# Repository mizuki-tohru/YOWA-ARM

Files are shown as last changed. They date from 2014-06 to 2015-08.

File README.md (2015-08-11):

YOWA-ARM
========

YOWA-ARM (Weak arm) is a robotic arm that can be used in the side of the human. No strength to hurt a person, this is a weak arm. This can not lift heavy objects. but, for example, push of a button work, only has a light work, is available for these. 
Inexpensive, but YOWA-ARM is a robot arm that could work. It has a working radius of the length of the human arm, and in harmony with the work environment for human beings. YOWA-ARM is not a toy. However, it is very inexpensive.
"How supposing I have one more arm." Do you have any kind of experience?
 YOWA-ARM can also perform the useless work which pushes a button without a repetition rest. 

YOWA-ARM is a specification based on the "Technical guidelines related to safety standards, such as the use of industrial robot, and, notice that define the Japan mechanical Minister of Health, Labour and Welfare pursuant to the provisions of Article 36-31 issue the Ordinance on Industrial Safety and Health".
There is only output of 80 watts or less, and meets the safety measures each. Maximum output does not exceed 150 Newton. Therefore, the safety fence is not required for YOWA-ARM.
Also, as a safety measure, It install a sensor for detecting a human body around the arm tip. Then, the arm will decelerate to avoid the rapid collision of the human body.
Exposes all the design data, YOWA-ARM can be manufactured by anyone.

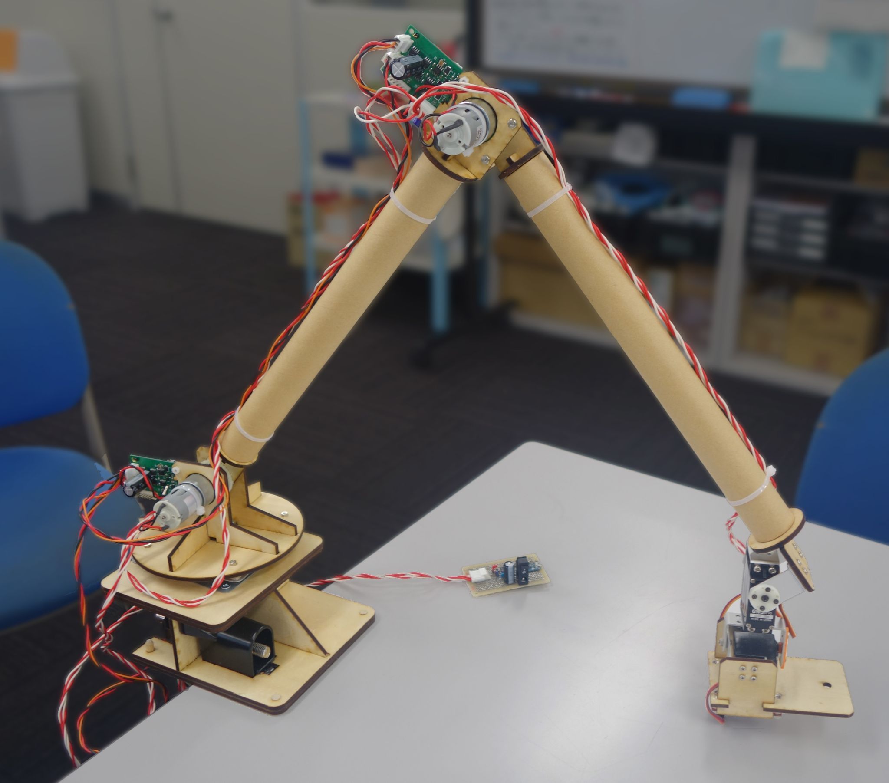
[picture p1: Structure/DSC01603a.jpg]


　YOWA-ARM(よわアーム)は、人間のそばで使えるロボットアームです。人を傷つけるような強さの無い、弱いアームです。重いものを持つことは出来ませんが、ちょっとボタンを押すだけ、とか、ちょっとライトを持っているだけ、といった作業は出来ます。
　YOWA-ARMはできるだけ安価に、でも仕事ができるロボットアームとして設計されました。人間の腕の長さの作業半径を持ち、人間用の作業環境にそのまま調和します。YOWA-ARMはオモチャじゃないロボットアームとしては破格に安価です。
　もう一本、手があったら、この作業もっと楽になるのに。そういう経験ありませんか？この仕事って結局ボタン押すだけ、そういう仕事ありませんか？YOWA-ARMはそういう仕事を疲れることなく繰り返し休み無くおこなえます。

　YOWA-ARMは、産業用ロボットの使用等の安全基準に関する技術上の指針、及び、労働安全衛生規則第三十六条第三十一号の規定に基づき厚生労働大臣が定める機械を定める告示、に基づき、80ワット以下の出力で各安全措置を満たした仕様です。また最大出力は150ニュートンを超えません。そのためこのYOWA-ARMは安全柵が不要です。
　また安全措置として、アーム先端部に周囲の人体を検出するセンサを搭載して、人体への急速な衝突を避けて減速します。
　YOWA-ARMは設計データを全て公開し、誰でも製造可能とします。

========

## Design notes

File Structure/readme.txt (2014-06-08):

Guidance of processing:
Use a plywood board (overlaid plywood, or MDF 4 mm in thickness). 
Data is AUTOCAD R13 ASCII format.

加工の手引き：
シナベニアまたはMDF 厚さ4mmの板を使用します。
データはAUTOCAD R13 ASCIIフォーマットとなっています。

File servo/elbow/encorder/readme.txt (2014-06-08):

Guidance of processing:

This is data of the optical encoder's codewheel of a through slits incremental quadrature type encoder.
To encorder_org_23.dxf which is a reflective slits, you paste together and create encorder_org_24.dxf of a transparent material.
I used the cutting plotter, Silhouette-Cameo for creation.
It reduce data to 1/6 after reading. Please reduce to 46% next after reducing to 36% first.

cutting parameter:
encorder_org_23.dxf
Material: Film label seal Silver thickness 0.07mm 
parameter: speed 4 thickness 7 Cutter 5 

encorder_org_24.dxf
 vinyl chloride board thickness 0.3mm
parameter: speed 1 thickness 24 Cutter 8 

加工の手引き:

これは透過型エンコーダの遮光円盤のデータです。
反射幕であるencorder_org_23.dxfに、透明な素材のencorder_org_24.dxfを張り合わせて作成します。
作成にはカッティングプロッタ、シルエットカメオを使用しました。
データは読み込み後1/6に縮小します。まず36%に縮小してから、次に46%に縮小してください。

加工パラメータは以下の通りです。
encorder_org_23.dxf
素材：エーワン N29283 フィルム・ラベルシール つや消し シルバー
パラメータ：速度4 厚さ7 カッター5

encorder_org_24.dxf
素材：塩ビ板 クリア 0.3mm
パラメータ：速度1 厚さ24 カッター8

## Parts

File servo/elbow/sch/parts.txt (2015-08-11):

Parts list
No				Name			note		number		buyer
U$12			STM32F373C					1			Digi-key
U$10			HEDS9701-C54    Encorder	1			Digi-key
U$5,U$6			IR2302S						2			Digi-key
Q1,Q2,Q3,Q4		FDS5680         FET			4			Akizuki(Akihabara)
U$7,U$17,U$18	4S69F           Inverter	3			Suzushou(Akihabara)
U$8				TAR5SB33		REG			1			Akizuki(Akihabara)
U$15     		NJM78L05UA      REG         1			Akizuki(Akihabara)
U$11			SN65HVD30       RS422drv	1			Digi-key
Q9				NX5032GA 8MHz	XTAL		1			Digi-key
Q10             32.768kHz       XTAL		1			Akizuki(Akihabara)
U$13,U$14       ACPL-M60L                   2			Digi-key
LED3,4      	LED SMD 0603    led			2			Akizuki(Akihabara)
D1,D4 	      	SX34F           diode		2			Akizuki(Akihabara)
D5       		1SS352         	diode		1			Akizuki(Akihabara)
U$16     		ZX62R-B-5P     	USB-MicroB	1			Akizuki(Akihabara)
L1              BLM21PG331SN    			1			Digi-key(or Akizuki)

C24,C25,C26,C27 7pF SMD 0603	cap			4			Suzushou(Akihabara)

C16,C29,C30,C31,C32
		    	0.01uF SMD 0603 cap			5			Sengoku(Akihabara)
C11,C12,C13,C17,C18,C19,C28,C34,C35,C40
       			0.1uF SMD 0603  cap			10			Sengoku(Akihabara)
C39      		0.33uF SMD 0603 cap         1			Suzushou(Akihabara)
C14      		1uF SMD 2012	cap			1			Akizuki(Akihabara)
C15      		4.7uF SMD 2012	cap			1			Akizuki(Akihabara)
C33,C41      	10uF SMD 3216	cap			2			Akizuki(Akihabara)
C6,C7       	22uF SMD 3225   cap			2			Akizuki(Akihabara)
C8  	     	470uF electrolytic cap		1			Sengoku(Akihabara)
R5,R6,R7,R8,R11,R19,R21,C21
				22ƒ¶ SMD 0603	regisiter	8			Sengoku(Akihabara)
R33,R34			27ƒ¶ SMD 0603	regisiter	2			Sengoku(Akihabara)
R23,R24			33ƒ¶ SMD 0603	regisiter	2			Sengoku(Akihabara)
R25	     	 	100ƒ¶ SMD 0603	regisiter	1			Sengoku(Akihabara)
R28				220ƒ¶ SMD 0603	regisiter	1			Sengoku(Akihabara)
R26,R27,R29,R30,R31,R32
			  	330ƒ¶ SMD 0603	regisiter	6			Sengoku(Akihabara)
R36,R37			470ƒ¶ SMD 0603	regisiter	2			Sengoku(Akihabara)
R35				1.5kƒ¶ SMD 0603	regisiter	1			Sengoku(Akihabara)
R1,R10,R22      10kƒ¶ SMD 0603	regisiter	3			Sengoku(Akihabara)

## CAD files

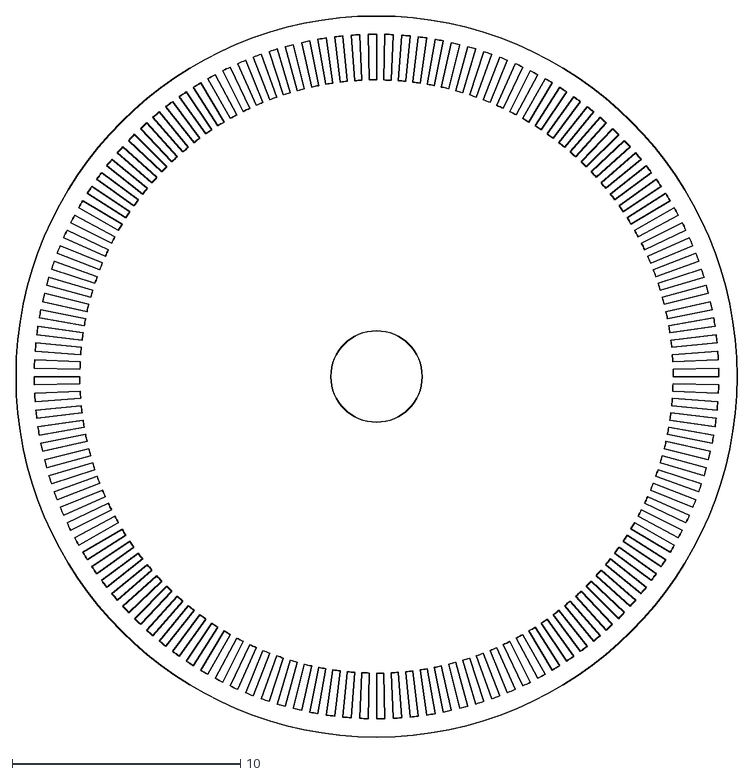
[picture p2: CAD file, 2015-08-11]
servo/elbow/encorder/encorder_org_26a.dxf
31.6 x 31.6

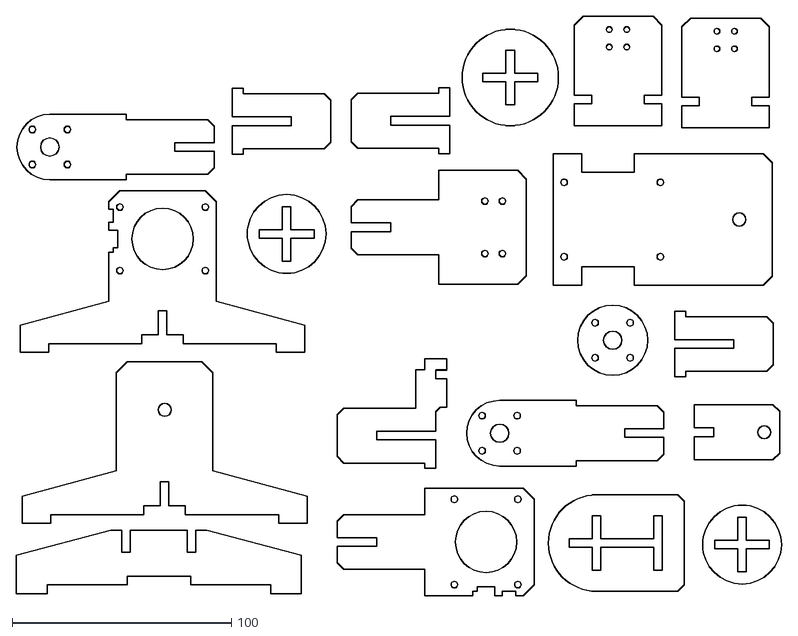
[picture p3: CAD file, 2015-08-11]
Structure/elbow_072_ascii.dxf
349.3 x 264.5

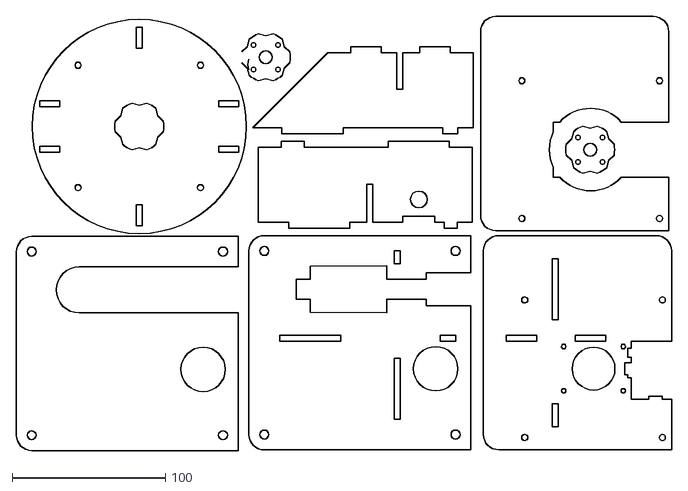
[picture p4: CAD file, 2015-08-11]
Structure/elbow_071a_ascii.dxf
428.2 x 283.7

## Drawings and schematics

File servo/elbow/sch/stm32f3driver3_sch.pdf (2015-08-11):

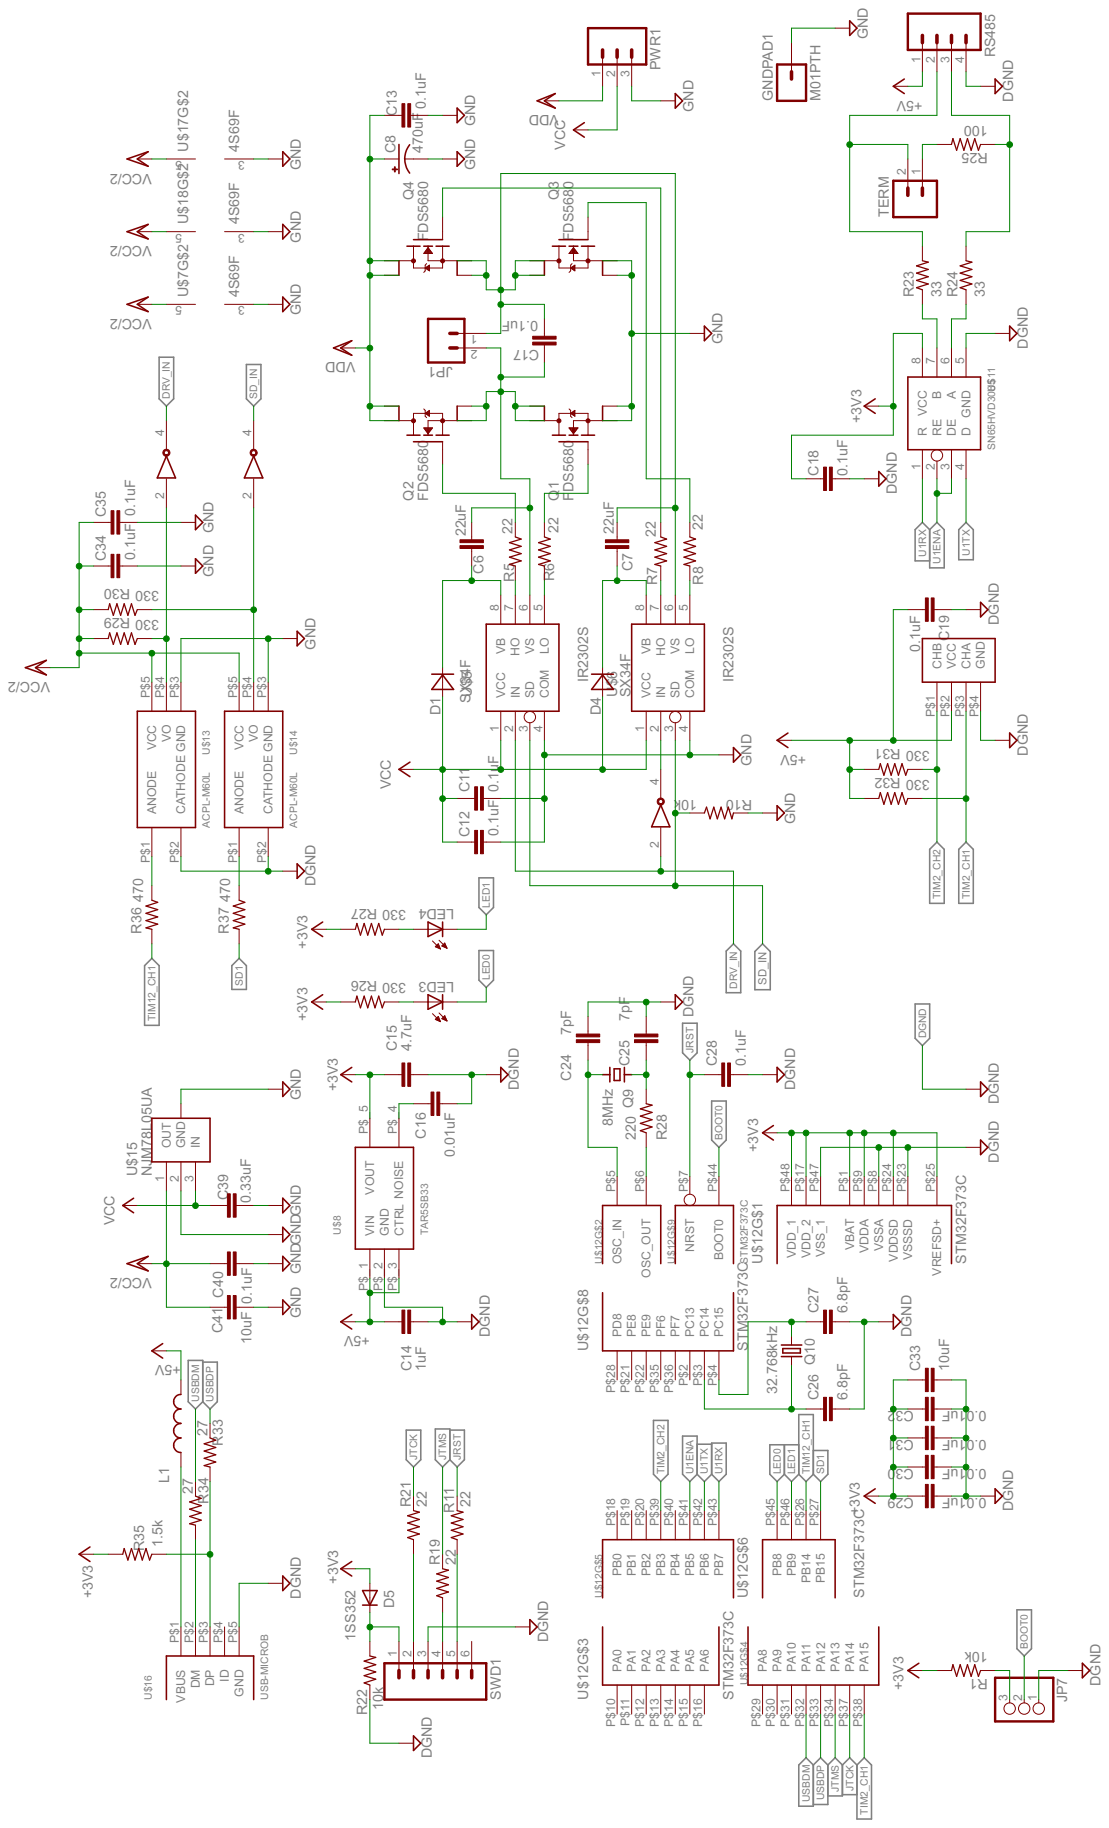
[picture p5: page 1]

0.33uF 0.1uF 10uF GND GND GND GND GND

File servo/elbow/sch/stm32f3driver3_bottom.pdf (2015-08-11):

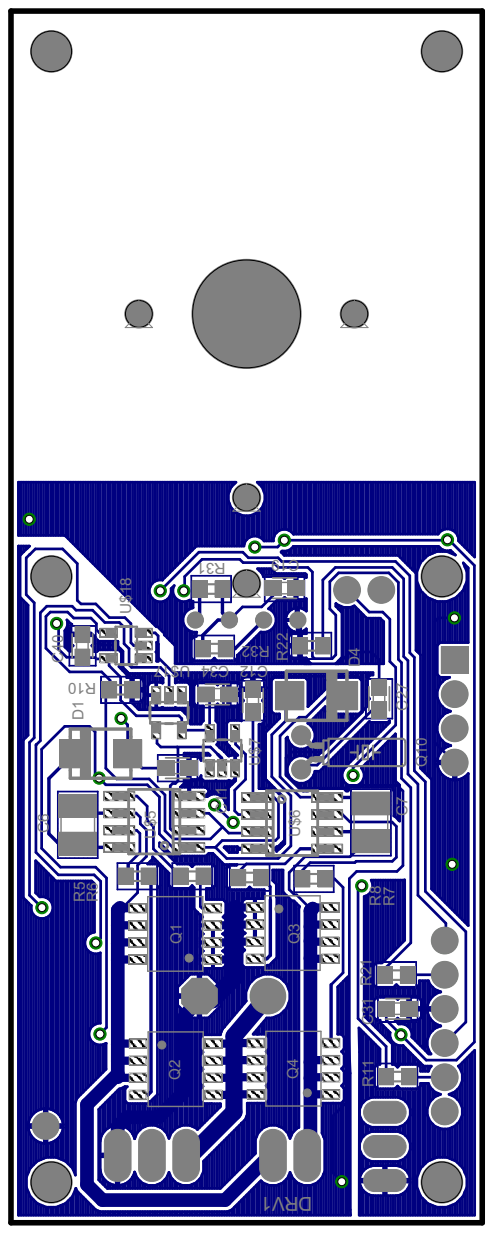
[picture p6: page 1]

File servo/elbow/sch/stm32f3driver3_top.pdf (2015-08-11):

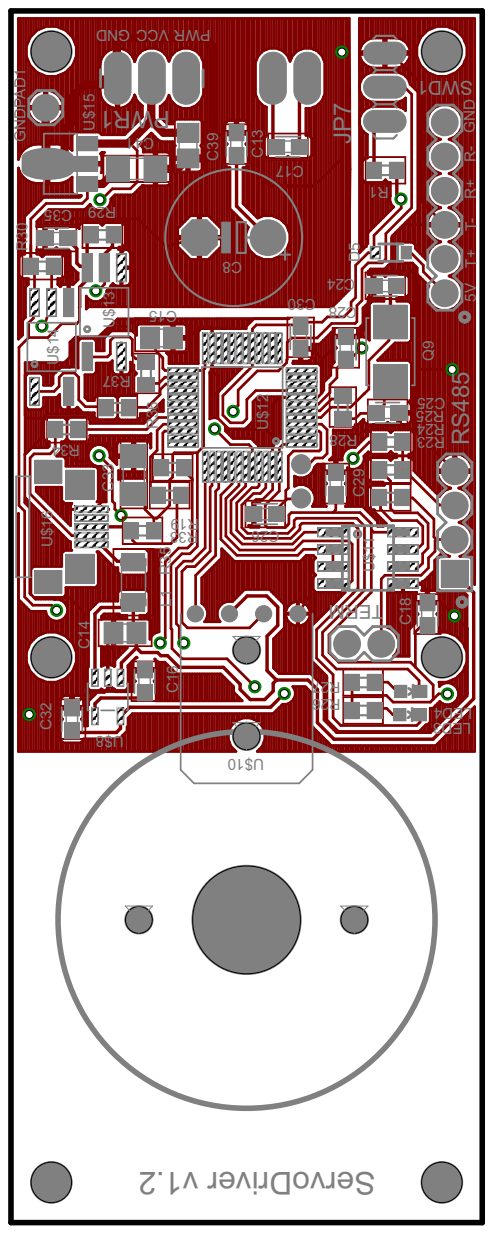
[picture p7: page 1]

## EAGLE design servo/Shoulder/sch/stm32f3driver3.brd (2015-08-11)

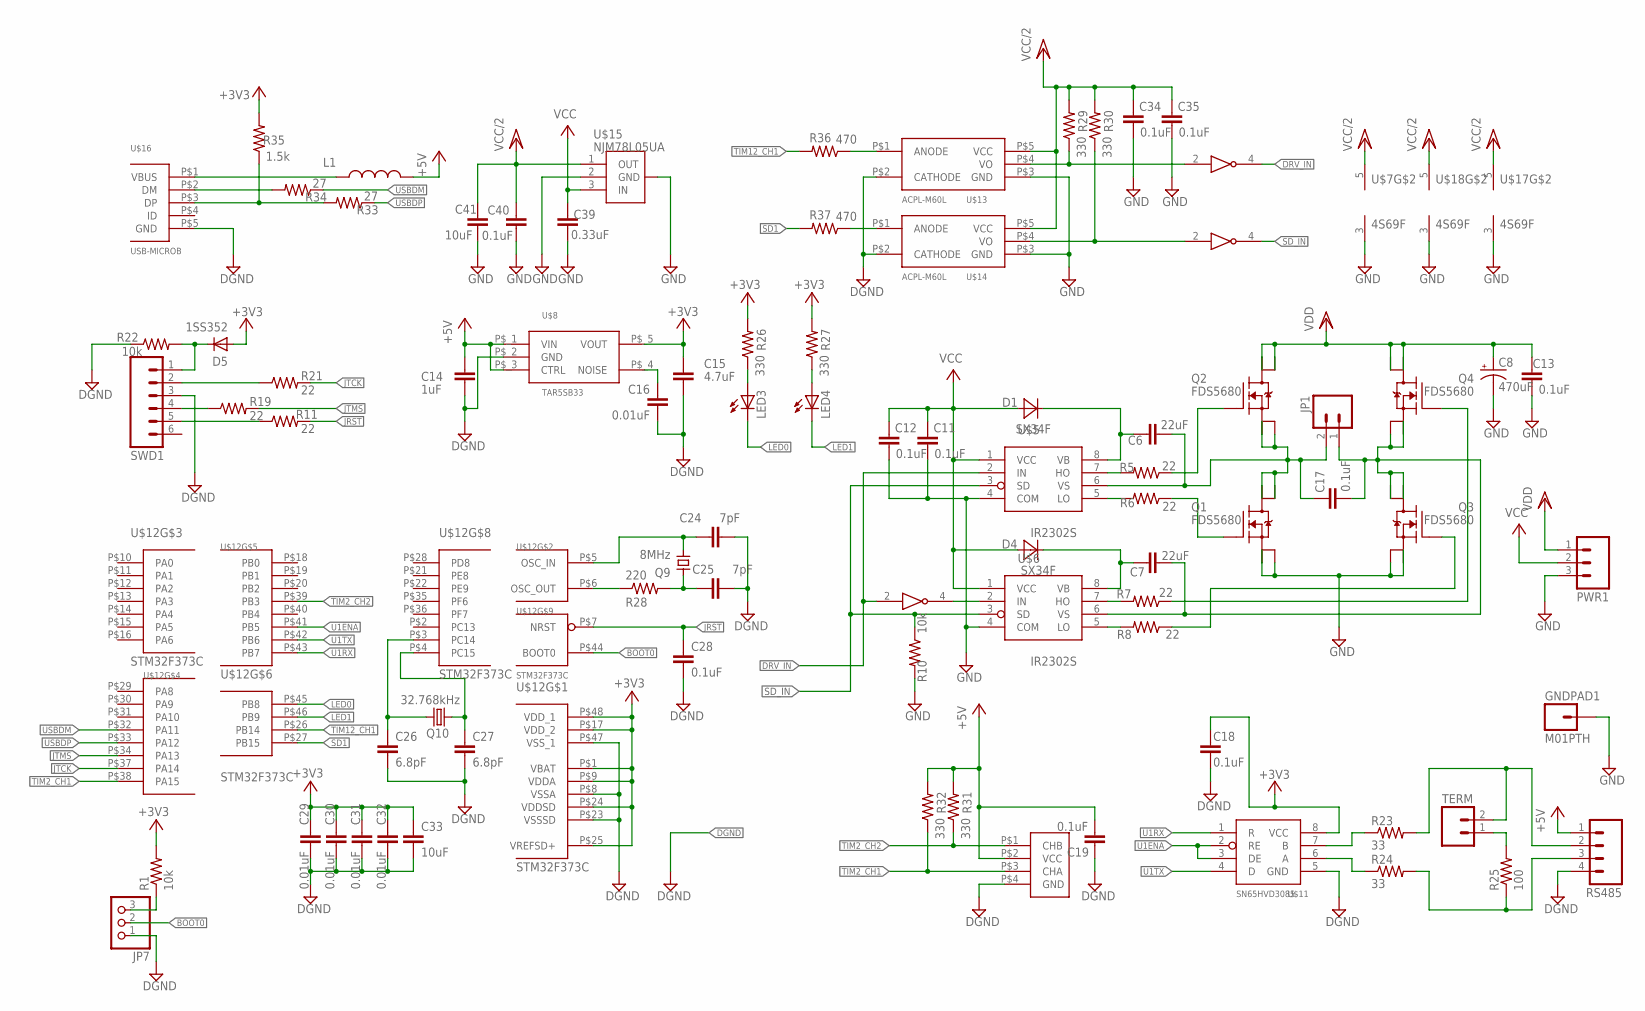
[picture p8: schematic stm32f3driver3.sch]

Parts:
C6, C7: 22uF; C3225
C8: 470uF; E5-10,5
C11, C12, C13, C17, C19, C28, C34, C35, C40: 0.1uF; C0603
C14: 1uF; C2012
C15: 4.7uF; C2012
C16, C29, C30, C31, C32: 0.01uF; C0603
C18: 0.1uF; C1608
C24, C25: 7pF; C0603
C26, C27: 6.8pF; C0603
C33, C41: 10uF; C3216
C39: 0.33uF; C0805
D1, D4: SX34F; SMA
D5: 1SS352; SOD-323
GNDPAD1: M01PTH; 1X01
JP1: M02PTH3; 1X02_LONGPADS
JP7: PINHD-1X3; 1X03
L1: L-USL3216C; L3216C
LED3, LED4: LED0603; LED-0603
PWR1: M03LONGPADS; 1X03_LONGPADS
Q1, Q2, Q3, Q4: FDS5680; 1206-8CHIP-FET
Q9: 8MHz; SMD5032
Q10: 32.768kHz; TC26H
R1, R10, R22: 10k; R0603
R5, R6, R7, R8, R11, R19, R21: 22; R0603
R23, R24: 33; R0603
R25: 100; R0603
R26, R27, R29, R30, R31, R32: 330; R0603
R28: 220; R0603
R33, R34: 27; R0603
R35: 1.5k; R0603
R36, R37: 470; R0603
RS485: M04PTH; 1X04
SWD1: M06SIP; 1X06
TERM: M02PTH; 1X02
U$5, U$6: IR2302S; SO8
U$7, U$17, U$18: 4S69F; SOT23-5
U$8: TAR5SB33
U$10: HEDS9701-C54; HEDS9701
U$11: SN65HVD3085; SO8
U$12: STM32F373C; TQFP48
U$13, U$14: ACPL-M60L; SO5
U$15: NJM78L05UA; SOT89
U$16: USB-MICROB; USB_MICROB

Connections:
+3V3: C15.1, C18.1, C29.1, C30.1, C31.1, C32.1, C33.1, D5.2 (A), R1.2, R26.2, R27.2, R35.2, U$8.P$_5 (VOUT), U$11.8 (VCC), U$12.P$1 (VBAT), U$12.P$9 (VDDA), U$12.P$17 (VDD_2), U$12.P$24 (VDDSD), U$12.P$25 (VREFSD+), U$12.P$48 (VDD_1)
+5V: C14.1, C19.2, L1.2, R31.2, R32.2, RS485.1, U$8.P$_1 (VIN), U$8.P$_3 (CTRL), U$10.P$2 (VCC)
BOOT0: JP7.2, U$12.P$44 (BOOT0)
DGND: C14.2, C15.2, C16.2, C18.2, C19.1, C24.2, C25.2, C26.2, C27.2, C28.2, C29.2, C30.2, C31.2, C32.2, C33.2, JP7.1, R22.1, RS485.4, SWD1.3, U$8.P$_2 (GND), U$10.P$4 (GND), U$11.5 (GND), U$12.P$8 (VSSA), U$12.P$23 (VSSSD), U$12.P$47 (VSS_1), U$13.P$2 (CATHODE), U$14.P$2 (CATHODE), U$16.P$5 (GND)
DRV_IN: U$5.2 (IN), U$7.2, U$17.4
GND: C8.-, C11.2, C12.2, C13.2, C34.2, C35.2, C39.2, C40.2, C41.2, GNDPAD1.1, PWR1.3, Q1.1 (S), Q1.2 (S1), Q1.3 (S2), Q3.1 (S), Q3.2 (S1), Q3.3 (S2), R10.2, U$5.4 (COM), U$6.4 (COM), U$7.3 (V-), U$13.P$3 (GND), U$14.P$3 (GND), U$15.2 (GND), U$15.2@1 (GND2), U$17.3 (V-), U$18.3 (V-)
JRST: C28.1, R11.2, U$12.P$7 (NRST)
JTCK: R21.2, U$12.P$37 (PA14)
JTMS: R19.2, U$12.P$34 (PA13)
LED0: LED3.C, U$12.P$45 (PB8)
LED1: LED4.C, U$12.P$46 (PB9)
unnamed: C7.1, D4.C, U$6.8 (VB)
unnamed: C7.2, C17.2, JP1.1, Q3.5 (D), Q3.6 (D1), Q3.7 (D2), Q3.8 (D3), Q4.1 (S), Q4.2 (S1), Q4.3 (S2), U$6.6 (VS)
unnamed: C6.2, C17.1, JP1.2, Q1.5 (D), Q1.6 (D1), Q1.7 (D2), Q1.8 (D3), Q2.1 (S), Q2.2 (S1), Q2.3 (S2), U$5.6 (VS)
unnamed: C6.1, D1.C, U$5.8 (VB)
unnamed: R5.2, U$5.7 (HO)
unnamed: R6.2, U$5.5 (LO)
unnamed: R7.2, U$6.7 (HO)
unnamed: R8.2, U$6.5 (LO)
unnamed: Q2.4 (G), R5.1
unnamed: Q4.4 (G), R7.1
unnamed: Q3.4 (G), R8.1
unnamed: U$6.2 (IN), U$7.4
unnamed: Q1.4 (G), R6.1
unnamed: D5.1 (C), R22.2, SWD1.1
unnamed: R21.1, SWD1.2
unnamed: R19.1, SWD1.4
unnamed: R11.1, SWD1.5
unnamed: C16.1, U$8.P$_4 (NOISE)
unnamed: LED3.A, R26.1
unnamed: LED4.A, R27.1
unnamed: R23.1, U$11.7 (B)
unnamed: R24.1, U$11.6 (A)
unnamed: R24.2, R25.1, RS485.3
unnamed: R23.2, RS485.2, TERM.2
unnamed: R25.2, TERM.1
unnamed: R28.1, U$12.P$6 (OSC_OUT)
unnamed: C25.1, Q9.P1, R28.2
unnamed: C24.1, Q9.P2, U$12.P$5 (OSC_IN)
unnamed: C27.1, Q10.2, U$12.P$4 (PC15)
unnamed: C26.1, Q10.1, U$12.P$3 (PC14)
unnamed: R34.2, U$16.P$2 (DM)
unnamed: R33.2, R35.1, U$16.P$3 (DP)
unnamed: L1.1, U$16.P$1 (VBUS)
unnamed: R29.1, U$13.P$4 (VO), U$17.2
unnamed: R30.1, U$14.P$4 (VO), U$18.2
unnamed: R37.1, U$14.P$1 (ANODE)
unnamed: R36.1, U$13.P$1 (ANODE)
unnamed: JP7.3, R1.1
SD1: R37.2, U$12.P$27 (PB15)
SD_IN: R10.1, U$5.3 (SD), U$6.3 (SD), U$18.4
TIM2_CH1: R32.1, U$10.P$3 (CHA), U$12.P$38 (PA15)
TIM2_CH2: R31.1, U$10.P$1 (CHB), U$12.P$39 (PB3)
TIM12_CH1: R36.2, U$12.P$26 (PB14)
U1ENA: U$11.2 (RE), U$11.3 (DE), U$12.P$41 (PB5)
U1RX: U$11.1 (R), U$12.P$43 (PB7)
U1TX: U$11.4 (D), U$12.P$42 (PB6)
USBDM: R34.1, U$12.P$32 (PA11)
USBDP: R33.1, U$12.P$33 (PA12)
VCC: C11.1, C12.1, C39.1, D1.A, D4.A, PWR1.2, U$5.1 (VCC), U$6.1 (VCC), U$15.3 (IN)
VCC/2: C34.1, C35.1, C40.1, C41.1, R29.2, R30.2, U$7.5 (V+), U$13.P$5 (VCC), U$14.P$5 (VCC), U$15.1 (OUT), U$17.5 (V+), U$18.5 (V+)
VDD: C8.+, C13.1, PWR1.1, Q2.5 (D), Q2.6 (D1), Q2.7 (D2), Q2.8 (D3), Q4.5 (D), Q4.6 (D1), Q4.7 (D2), Q4.8 (D3)

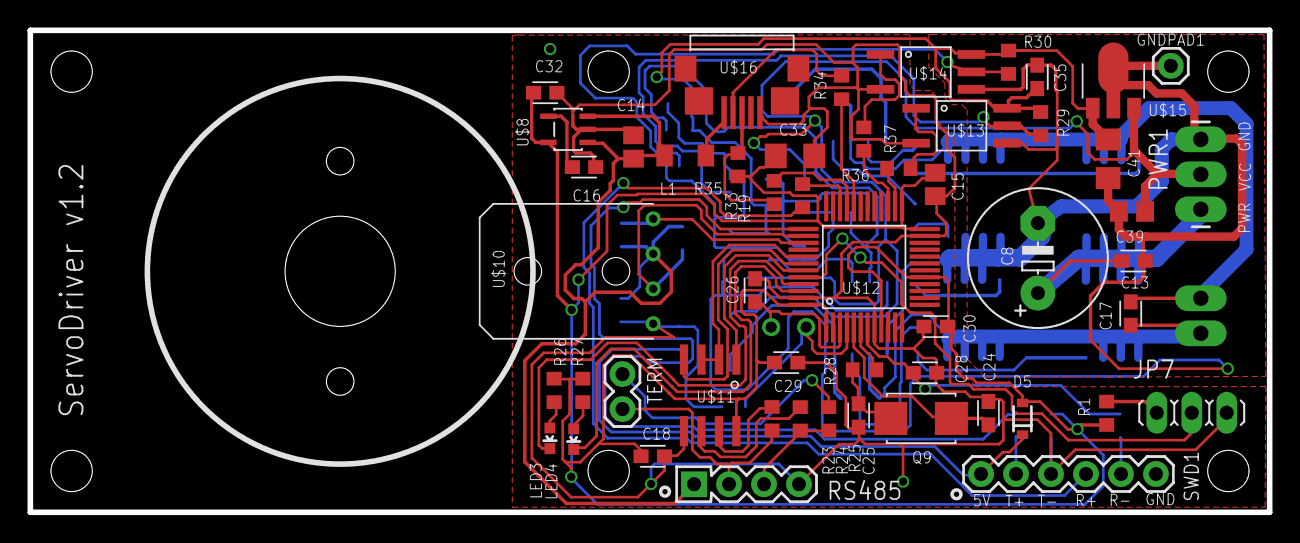
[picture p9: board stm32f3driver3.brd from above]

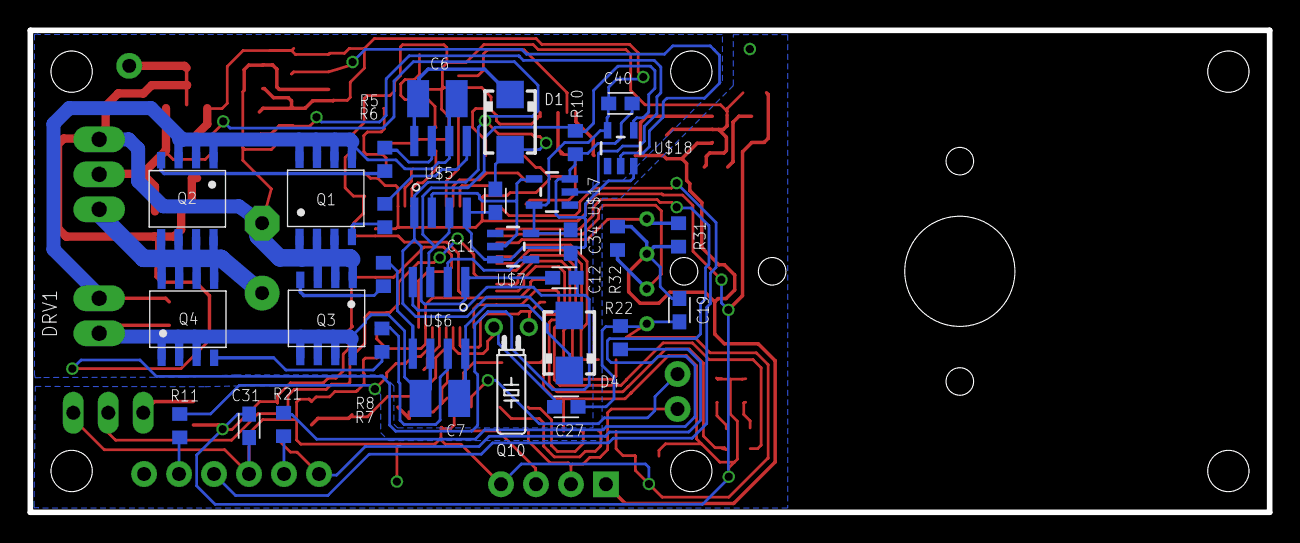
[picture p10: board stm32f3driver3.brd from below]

Board: 2 copper layers, 90.0 x 35.0 mm, 84 parts (31 on the bottom side), 62 nets.

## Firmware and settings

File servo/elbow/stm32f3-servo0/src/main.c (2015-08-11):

/**
  ******************************************************************************
  * @file    Project/STM32F37x_StdPeriph_Templates/main.c 
  * @author  MCD Application Team
  * @version V1.0.0
  * @date    20-September-2012
  * @brief   Main program body
  ******************************************************************************
  * @attention
  *
  * <h2><center>&copy; COPYRIGHT 2012 STMicroelectronics</center></h2>
  *
  * Licensed under MCD-ST Liberty SW License Agreement V2, (the "License");
  * You may not use this file except in compliance with the License.
  * You may obtain a copy of the License at:
  *
  *        http://www.st.com/software_license_agreement_liberty_v2
  *
  * Unless required by applicable law or agreed to in writing, software 
  * distributed under the License is distributed on an "AS IS" BASIS, 
  * WITHOUT WARRANTIES OR CONDITIONS OF ANY KIND, either express or implied.
  * See the License for the specific language governing permissions and
  * limitations under the License.
  *
  ******************************************************************************
  */

/* Includes ------------------------------------------------------------------*/
#include "main.h"
#include "math.h"
#include "stm32f37x.h"
//#include "platform_config.h"
//#include "hw_config.h"
#include "stm32f37x_conf.h"
//#include "i2c.h"
/* Scheduler includes. */
#include "FreeRTOS.h"
#include "semphr.h"
#include "task.h"
#include "queue.h"
#include "control.h"

#include "hw_config.h"
#include "usb_lib.h"
#include "usb_desc.h"
#include "usb_pwr.h"
#include "systick.h"

//#include "lsm9ds0.h"
//#include "accTask.h"
#include "dcmotor_controller.h"
#include "task_sequence.h"
#include "task_control.h"
#include "quaternion.h"
#include "encoder.h"

// IO Pin
// PA11 USB    AF14
// PA12 USB    AF14
// PA13 JTMS   AF0
// PA14 JTCK   AF0
// PA15 TIM2_CH1 AF1     ENCORDER
// PB3  TIM2_CH2 AF1     ENCORDER
// PB5  U1ENA  I/O OUT
// PB6  U1TX   AF7
// PB7  U1RX   AF7
// PB8  LED0   I/O OUT
// PB9  LED1   I/O OUT
// PB14 TIM12_CH1 AF9
// PB15 SD1    I/O OUT(TIM12_CH2 AF9)

/** @addtogroup Template_Project
  * @{
  */

/* Private typedef -----------------------------------------------------------*/
/* Private define ------------------------------------------------------------*/

#define MESSAGE1   "STM32F37x CortexM4  " 
#define MESSAGE2   " Device running on  " 
#define MESSAGE3   "   STM32373C-EVAL   " 


#define   ENC_FILTER              6
#define   MAX_COUNT               1200
#define   TIM1_PERIOD      (MAX_COUNT*3)

#define LIMIT_XY_ROTATE			10.f

#define STACK_SIZE_MIN	128	/* usStackDepth	- the stack size DEFINED IN WORDS.*/
float temp1 = 0.0f;
int tmpflg = 0;

void vLedBlinkBlue(void *pvParameters);
void vLedBlinkRed(void *pvParameters);

/* Private macro -------------------------------------------------------------*/
/* Private variables ---------------------------------------------------------*/
//USART_InitTypeDef USART_InitStructure;
RCC_ClocksTypeDef RCC_Clocks;

//static __IO uint32_t TimingDelay;
unsigned long count_data=0;
char buf[20];

xSemaphoreHandle xSemaphore = NULL;

/* Functions -----------------------------------------------------------------*/
//static void vSensorTask( void *pvParameters );
static void vControlTask( void *pvParameters );

xTaskHandle xCreatedTask;
unsigned long ulMemCheckTaskRunningCount;

uint8_t status_LED1 = 0;
uint8_t status_LED2 = 0;

extern __IO uint8_t Receive_Buffer[64];
extern __IO  uint32_t Receive_length ;
extern __IO  uint32_t length ;
uint8_t Send_Buffer[64];
uint32_t packet_sent=1;
uint32_t packet_receive=1;

//char encbuf[10];

/* Private function prototypes -----------------------------------------------*/
#ifdef __GNUC__
/* With GCC/RAISONANCE, small printf (option LD Linker->Libraries->Small printf
   set to 'Yes') calls __io_putchar() */
#define PUTCHAR_PROTOTYPE int __io_putchar(int ch)
#else
#define PUTCHAR_PROTOTYPE int fputc(int ch, FILE *f)
#endif /* __GNUC__ */

#if 0
//------------------------------------------------------------------------
//	long値実数から16進ASCIIへ。ltoa()を使わないのは、出力を大文字にしたい
//だけの理由から
//------------------------------------------------------------------------
int ltohex(unsigned long l,unsigned char * buf,unsigned char i)
{
	int j,k;
	unsigned long x;
	for(j = 0;j < i;j++) {
		x = l;
		for (k = 0;k < (i - j - 1);k++) x = (x >> 4);
		buf[j] = "0123456789ABCDEF"[(x & 0x0f)];
	}
	buf[j] = 0;
	return j;
}
#endif

/* Private functions ---------------------------------------------------------*/
void IOInit(void)
{
	GPIO_InitTypeDef  GPIO_InitStructure;
  
  /* Enable the GPIO_A Clock */
	RCC_AHBPeriphClockCmd(RCC_AHBPeriph_GPIOA, ENABLE);
	
  /* Configure the GPIO_A pin */
	GPIO_InitStructure.GPIO_Pin = GPIO_Pin_15;
	GPIO_InitStructure.GPIO_Mode = GPIO_Mode_IN;
	GPIO_InitStructure.GPIO_PuPd = GPIO_PuPd_NOPULL;
	GPIO_InitStructure.GPIO_Speed = GPIO_Speed_50MHz;
	GPIO_Init(GPIOA, &GPIO_InitStructure);
	
	GPIO_InitStructure.GPIO_Pin = GPIO_Pin_11|GPIO_Pin_12|GPIO_Pin_13|GPIO_Pin_14|GPIO_Pin_15;
	GPIO_InitStructure.GPIO_Mode = GPIO_Mode_AF;
	GPIO_InitStructure.GPIO_Speed = GPIO_Speed_50MHz;
	GPIO_InitStructure.GPIO_OType = GPIO_OType_PP;
	GPIO_InitStructure.GPIO_PuPd = GPIO_PuPd_UP;
	GPIO_Init(GPIOA, &GPIO_InitStructure);
	
	GPIO_PinAFConfig(GPIOA, GPIO_PinSource11, GPIO_AF_14);/*USB*/
	GPIO_PinAFConfig(GPIOA, GPIO_PinSource12, GPIO_AF_14);/*USB*/
	GPIO_PinAFConfig(GPIOA, GPIO_PinSource13, GPIO_AF_0);/*JTMS*/
	GPIO_PinAFConfig(GPIOA, GPIO_PinSource14, GPIO_AF_0);/*JTCK*/
	GPIO_PinAFConfig(GPIOA, GPIO_PinSource15, GPIO_AF_1);/*TIM2_Ch1*/

	/* Enable the GPIO_B Clock */
	RCC_AHBPeriphClockCmd(RCC_AHBPeriph_GPIOB, ENABLE);
	
	GPIO_InitStructure.GPIO_Pin = GPIO_Pin_3;
	GPIO_InitStructure.GPIO_Mode = GPIO_Mode_IN;
	GPIO_InitStructure.GPIO_PuPd = GPIO_PuPd_NOPULL;
	GPIO_InitStructure.GPIO_Speed = GPIO_Speed_50MHz;
	GPIO_Init(GPIOB, &GPIO_InitStructure);

  /* Configure the GPIO_B pin */
	GPIO_InitStructure.GPIO_Pin = GPIO_Pin_5|GPIO_Pin_8|GPIO_Pin_9|GPIO_Pin_14|GPIO_Pin_15;
//	GPIO_InitStructure.GPIO_Pin = GPIO_Pin_5|GPIO_Pin_8|GPIO_Pin_9;
	GPIO_InitStructure.GPIO_Mode = GPIO_Mode_OUT;
	GPIO_InitStructure.GPIO_OType = GPIO_OType_PP;
	GPIO_InitStructure.GPIO_PuPd = GPIO_PuPd_NOPULL;
	GPIO_InitStructure.GPIO_Speed = GPIO_Speed_50MHz;
	GPIO_Init(GPIOB, &GPIO_InitStructure);
	
	GPIO_InitStructure.GPIO_Pin = GPIO_Pin_3|GPIO_Pin_6|GPIO_Pin_7|GPIO_Pin_14;
//	GPIO_InitStructure.GPIO_Pin = GPIO_Pin_3|GPIO_Pin_6|GPIO_Pin_7|GPIO_Pin_14|GPIO_Pin_15;
	GPIO_InitStructure.GPIO_Mode = GPIO_Mode_AF;
	GPIO_InitStructure.GPIO_Speed = GPIO_Speed_50MHz;
	GPIO_InitStructure.GPIO_OType = GPIO_OType_PP;
	GPIO_InitStructure.GPIO_PuPd = GPIO_PuPd_UP;
	GPIO_Init(GPIOB, &GPIO_InitStructure);
	
	GPIO_PinAFConfig(GPIOB, GPIO_PinSource3,  GPIO_AF_1);/*TIM2_CH2*/
	GPIO_PinAFConfig(GPIOB, GPIO_PinSource6,  GPIO_AF_7);/*U1_TX*/
	GPIO_PinAFConfig(GPIOB, GPIO_PinSource7,  GPIO_AF_7);/*U1_RX*/
	GPIO_PinAFConfig(GPIOB, GPIO_PinSource14, GPIO_AF_9);/*TIM12_CH1*/
//	GPIO_PinAFConfig(GPIOB, GPIO_PinSource15, GPIO_AF_9);/*TIM12_CH2*/
}

void TIMInit()
{
	TIM_TimeBaseInitTypeDef  TIM_TimeBaseStructure;
 	TIM_OCInitTypeDef  TIM_OCInitStructure;
 	TIM_ICInitTypeDef  TIM_ICInitStructure;
 	/* TIM2 clock enable */
    RCC_APB1PeriphClockCmd(RCC_APB1Periph_TIM2, ENABLE);
	/* TIM12 clock enable */
    RCC_APB1PeriphClockCmd(RCC_APB1Periph_TIM12, ENABLE);

//	uint16_t PrescalerValue = (uint16_t) ((SystemCoreClock /2) / 1000000) - 1;
	uint16_t PrescalerValue2 = (uint16_t) ((SystemCoreClock / 2) / 5000000) - 1;
 	uint16_t PrescalerValue = (uint16_t) ((SystemCoreClock ) / 7200000) - 1;

	/* Time base configuration */
	TIM_TimeBaseStructure.TIM_Prescaler = 0;
	TIM_TimeBaseStructure.TIM_Period = 0xffff;
	TIM_TimeBaseStructure.TIM_ClockDivision = 0;
	TIM_TimeBaseStructure.TIM_CounterMode = TIM_CounterMode_Up;
	TIM_TimeBaseInit(TIM2, &TIM_TimeBaseStructure);
	
//	TIM_PrescalerConfig(TIM2, PrescalerValue, TIM_PSCReloadMode_Immediate);
	TIM_PrescalerConfig(TIM2, 0, TIM_PSCReloadMode_Immediate);
	TIM_EncoderInterfaceConfig(TIM2,TIM_EncoderMode_TI12,
		TIM_ICPolarity_Rising, TIM_ICPolarity_Rising);
		
	TIM_ICStructInit(&TIM_ICInitStructure);
	TIM_ICInitStructure.TIM_ICFilter = ENC_FILTER;//ICx_FILTER;
	TIM_ICInit(TIM2, &TIM_ICInitStructure);
	TIM2->CNT = 0;
//  TIM_SetAutoreload (TIM2, 0xffff);
	
	/* Time base configuration */
	TIM_TimeBaseStructure.TIM_Period = 7200;
//	TIM_TimeBaseStructure.TIM_Prescaler = 100;
	TIM_TimeBaseStructure.TIM_Prescaler = PrescalerValue2;
	TIM_TimeBaseStructure.TIM_ClockDivision = 0;
	TIM_TimeBaseStructure.TIM_CounterMode = TIM_CounterMode_Up;
	TIM_TimeBaseInit(TIM12, &TIM_TimeBaseStructure);
	/* Output Compare Timing Mode configuration: Channel1 */
	TIM_OCInitStructure.TIM_OCMode = TIM_OCMode_PWM1;
	TIM_OCInitStructure.TIM_OutputState = TIM_OutputState_Enable;
	TIM_OCInitStructure.TIM_Pulse = 0;
	TIM_OCInitStructure.TIM_OCPolarity = TIM_OCPolarity_Low;
	TIM_OC1Init(TIM12, &TIM_OCInitStructure);
	TIM_OC2Init(TIM12, &TIM_OCInitStructure);
	TIM_OC3Init(TIM12, &TIM_OCInitStructure);
	TIM_OC4Init(TIM12, &TIM_OCInitStructure);
	TIM_OC1PreloadConfig(TIM12, TIM_OCPreload_Enable);
//	TIM_OC1PreloadConfig(TIM12, TIM_OCPreload_Disable);
	TIM_ARRPreloadConfig(TIM12, ENABLE);

	TIM_Cmd(TIM2, ENABLE);
	TIM_Cmd(TIM12, ENABLE);

}

void setPWM12(uint32_t i)
{
   TIM_SetCompare1(TIM12,i);
// TIM_SetCompare2(TIM12,i);
}


void dcmotor_on(bool on) {
	if (on) {
		GPIO_SetBits(GPIOB,GPIO_Pin_15);
	} else {
		GPIO_ResetBits(GPIOB,GPIO_Pin_15);
	}
}

void vApplicationIdleHook( void )
{
	
	while(1);
}

void vApplicationTickHook( void )
{
	    //GPIOE->BRR = BSRR_VAL;

};
void vApplicationMallocFailedHook( void )
{
	
	while(1);
};

static void rotate_xy(float x_rotate_deg, float y_rotate_deg) {
	float x_rotate = DEG_TO_RAD(x_rotate_deg);
	float y_rotate = DEG_TO_RAD(y_rotate_deg);
	float a_arm_deg = RAD_TO_DEG(get_a_arm_agnle(x_rotate, y_rotate));
//    float b_arm_deg = RAD_TO_DEG(get_b_arm_agnle(x_rotate, y_rotate));
	dcmotorctrl_set_motor_a_deg(a_arm_deg);
//	dcmotorctrl_set_motor_b_deg(b_arm_deg);
}



/**
  * @brief  Retargets the C library printf function to the USART.
  * @param  None
  * @retval None
  */
PUTCHAR_PROTOTYPE
{
  /* Place your implementation of fputc here */
  /* e.g. write a character to the USART */
  USART_SendData(EVAL_COM1, (uint8_t) ch);

  /* Loop until the end of transmission */
  while (USART_GetFlagStatus(EVAL_COM1, USART_FLAG_TC) == RESET)
  {}

  return ch;
}

void vApplicationStackOverflowHook( TaskHandle_t pxTask, char *pcTaskName )
{
	/* This function will get called if a task overflows its stack.   If the
	parameters are corrupt then inspect pxCurrentTCB to find which was the
	offending task. */

	( void ) pxTask;
	( void ) pcTaskName;

	for( ;; );
}

#ifdef  USE_FULL_ASSERT

/**
  * @brief  Reports the name of the source file and the source line number
  *         where the assert_param error has occurred.
  * @param  file: pointer to the source file name
  * @param  line: assert_param error line source number
  * @retval None
  */
void assert_failed(uint8_t* file, uint32_t line)
{ 
  /* User can add his own implementation to report the file name and line number,
     ex: printf("Wrong parameters value: file %s on line %d\r\n", file, line) */

  /* Infinite loop */
  while (1)
  {
  }
}
#endif

/**
  * @}
  */

void vTerminalControlTask(void *param) {
	char str[128];
	xTaskHandle vTaskControlHandle = NULL;
	xTaskHandle vTaskSequenceHandle = NULL;
	xTaskHandle vTaskLoggerHandle = NULL;
	int status = 0;
	
	float x_rotate_deg = 0.f;
	float y_rotate_deg = 0.f;
	
	xprintf("[COMMAND] start");
	for (;;) {
		putch('>');
		putch(' ');
		getch(str);
		if (strcmp(str, "s") == 0) {
			if (status == 0) {
			//	xTaskCreate(vTaskLogger, "vTaskLogger", 1024, NULL, 3, &vTaskLoggerHandle);
			//	xTaskCreate(vTaskControl, "vTaskControl", 1024*2, NULL, 1, &vTaskControlHandle);
				status = 1;
				xprintf("[COMMAND] started.\n");
			} else {
				dcmotorctrl_stop();
				
				vTaskDelay(100 / portTICK_RATE_MS);
				
				if (vTaskControlHandle) {
					vTaskDelete(vTaskControlHandle);
					vTaskControlHandle = NULL; 
				}
				if (vTaskSequenceHandle) {
					vTaskDelete(vTaskSequenceHandle);
					vTaskSequenceHandle = NULL; 
				}
			//	if (vTaskLoggerHandle) {
			//		vTaskDelete(vTaskLoggerHandle);
			//		vTaskLoggerHandle = NULL; 
			//	}
				status = 0;
				xprintf("[COMMAND] stopped.\n");
			}
			continue;
		} else if (strcmp(str, "q") == 0) {
			if (status == 0) {
			//	xTaskCreate(vTaskLogger, "vTaskLogger", 1024, NULL, 3, &vTaskLoggerHandle);
				xTaskCreate(vSequenceControl, "vSequenceControl", 1024*2, NULL, 1, &vTaskSequenceHandle);
				status = 2;
				xprintf("[COMMAND] sequence started.\n");
			} else {
				dcmotorctrl_stop();

				vTaskDelay(100 / portTICK_RATE_MS);

				if (vTaskControlHandle) {
					vTaskDelete(vTaskControlHandle);
					vTaskControlHandle = NULL; 
				}
			//	if (vTaskLoggerHandle) {
			//		vTaskDelete(vTaskLoggerHandle);
			//		vTaskLoggerHandle = NULL; 
			//	}
				if (vTaskSequenceHandle) {
					vTaskDelete(vTaskSequenceHandle);
					vTaskSequenceHandle = NULL; 
				}
				status = 0;
				xprintf("[COMMAND] sequence stopped.\n");
			}
			continue;
		} else if (strncmp(str, "st", 2) == 0) {
			int y = 2001, m = 1, d = 1, hh = 0, mm = 0, ss = 0;
			sscanf(str + 3, "%d %d %d %d %d %d", &y, &m, &d, &hh, &mm, &ss);
		//	set_RTC(y, m, d, hh, mm, ss);
		//	put_current_time();
			continue;
		} else if (strcmp(str, "t") == 0) {
		//	put_current_time();
			continue;
		} else if (strcmp(str, "p") == 0) {
			dcmotorctrl_dump_params();
			xprintf("x_rotate_deg:%.3f y_rotate_deg:%.3f\n", x_rotate_deg, y_rotate_deg);
			sequence_dump();
			continue;
		} else if (strncmp(str, "a ", 2) == 0) { 
			char *end;
			const char *s = str + 2;
			float val = strtof(s, &end);
			if (end != s) {
				dcmotorctrl_set_motor_a_deg(val);
				continue;
			}
		} else if (strncmp(str, "b ", 2) == 0) { 
			char *end;
			const char *s = str + 2;
			float val = strtof(s, &end);
			if (end != s) {
//				dcmotorctrl_set_motor_b_deg(val);
				continue;
			}
		} else if (strncmp(str, "c ", 2) == 0) { 
			char *end;
			const char *s = str + 2;
			float val = strtof(s, &end);
			if (end != s) {
				dcmotorctrl_set_motor_a_deg(val);
//				dcmotorctrl_set_motor_b_deg(val);
				continue;
			}
		} else if (strncmp(str, "x ", 2) == 0) { 
			char *end;
			const char *s = str + 2;
			float val = strtof(s, &end);
			if (end != s) {
				x_rotate_deg = val;
				if (x_rotate_deg >  LIMIT_XY_ROTATE) x_rotate_deg =  LIMIT_XY_ROTATE;
				if (x_rotate_deg < -LIMIT_XY_ROTATE) x_rotate_deg = -LIMIT_XY_ROTATE;
				rotate_xy(x_rotate_deg, y_rotate_deg);
				continue;
			}
		} else if (strncmp(str, "y ", 2) == 0) { 
			char *end;
			const char *s = str + 2;
			float val = strtof(s, &end);
			if (end != s) {
				y_rotate_deg = val;
				if (y_rotate_deg >  LIMIT_XY_ROTATE) y_rotate_deg =  LIMIT_XY_ROTATE;
				if (y_rotate_deg < -LIMIT_XY_ROTATE) y_rotate_deg = -LIMIT_XY_ROTATE;
				rotate_xy(x_rotate_deg, y_rotate_deg);
				continue;
			}
		} else if (strncmp(str, "kp ", 3) == 0) { 
			char *end;
			const char *s = str + 3;
			float val = strtof(s, &end);
			if (end != s) {
				dcmotorctrl_set_kp(val);
				continue;
			}
		} else if (strncmp(str, "ki ", 3) == 0) { 
			char *end;
			const char *s = str + 3;
			float val = strtof(s, &end);
			if (end != s) {
				dcmotorctrl_set_ki(val);
				continue;
			}
		} else if (strncmp(str, "kd ", 3) == 0) { 
			char *end;
			const char *s = str + 3;
			float val = strtof(s, &end);
			if (end != s) {
				dcmotorctrl_set_kd(val);
				continue;
			}
		} else if (strncmp(str, "sr ", 3) == 0) { 
			char *end;
			const char *s = str + 3;
			float val = strtof(s, &end);
			if (end != s) {
				sequence_set_rate(val);
				continue;
			}
		} else if (strncmp(str, "sd ", 3) == 0) { 
			char *end;
			const char *s = str + 3;
			float val = strtof(s, &end);
			if (end != s) {
				sequence_set_duration(val);
				continue;
			}
		} else if (strncmp(str, "sa ", 3) == 0) { 
			char *end;
			const char *s = str + 3;
			float val = strtof(s, &end);
			if (end != s) {
				sequence_set_max_angle_deg(val);
				continue;
			}
		}
		
		if (str[0] != '\0') {
			xprintf("unknown command: %s\n", str);
		}
	}
}

static void vControlTask( void *pvParameters )
{
	GPIO_SetBits(GPIOB,GPIO_Pin_8);
	GPIO_ResetBits(GPIOB,GPIO_Pin_9);
	for( ;; ){
		Delay(100);
	}
}
void vLedBlinkBlue(void *pvParameters)
{
	for(;;)
	{
	/* Set PE14 and PE15 */
	GPIOB->BSRR = GPIO_Pin_8;  
//    GPIOE->BSRR |= 0xC000;
		    		vTaskDelay( 500 / portTICK_RATE_MS );
//    GPIOE->BRR |= 0xC000;
	GPIOB->BRR = GPIO_Pin_8;  

		if(tmpflg){
			temp1 = temp1 - 15.0;
			if(temp1 < -44.0)tmpflg = 0;
		}else{
			temp1 = temp1 + 15.0;
			if(temp1 > 44.0)tmpflg = 1;
		}
		
    /* Reset PE14 and PE15 */
    		vTaskDelay( 500 / portTICK_RATE_MS );
//   		dcmotor_set_a(temp1 & 0xffff);
   	//	setPWM12(temp1 & 0xffff);
//   		dcmotor_set_a(temp1 & 0xffff);

		dcmotorctrl_set_motor_a_deg(temp1);

	}
}

void vLedBlinkRed(void *pvParameters)
{
	long encd;
	for(;;)
	{
	/* Set PE14 and PE15 */
	GPIOB->BSRR = GPIO_Pin_9;  
//    GPIOE->BSRR |= 0x3000;
		    		vTaskDelay( 500 / portTICK_RATE_MS );
//    GPIOE->BRR |= 0x3000;
	GPIOB->BRR = GPIO_Pin_9;  
    /* Reset PE14 and PE15 */
   		vTaskDelay( 500 / portTICK_RATE_MS );
//	CDC_Send_DATA ("OK ",3);
	//	encoder_sampling();
	//	encd = encoder_get_a();
//		encd = TIM_GetCounter(TIM2);
	//512パルスで一回転
//		ltohex(encd,encbuf,8);
//		encbuf[8] = ' ';
//		encbuf[9] = 0;
//		CDC_Send_DATA (encbuf,9);
	}
}

/**
  * @brief  Main program.
  * @param  None
  * @retval None
  */
int main(void)
{
	float i;
  /*!< At this stage the microcontrollers clock setting is already configured, 
       this is done through SystemInit() function which is called from startup
       file (startup_stm32f37x.s) before to branch to application main.
       To reconfigure the default setting of SystemInit() function, refer to
       system_stm32f37x.c file
     */ 
  /* SysTick end of count event each 10ms */
	Set_System();
//    NVIC_SetVectorTable(NVIC_VectTab_FLASH, 0x0000);
	
	RCC_GetClocksFreq(&RCC_Clocks);
	SystemCoreClockUpdate();
	SysTick_CLKSourceConfig( SysTick_CLKSource_HCLK );
	SysTick_Config(RCC_Clocks.HCLK_Frequency / 100);

	NVIC_SetPriority(SysTick_IRQn, 0x0);	
 	NVIC_PriorityGroupConfig( NVIC_PriorityGroup_4 );
 	
//	SysTick_Config(RCC_Clocks.HCLK_Frequency / 1000);

//	NVIC_SetVectorTable(NVIC_VectTab_FLASH, 0x0000);
//	NVIC_PriorityGroupConfig( NVIC_PriorityGroup_4 );
	
	/* Configure HCLK clock as SysTick clock source. */
	/* Set SysTickCounter for _delay_ms(); */
//	SysTickInit(100);
//	SysTickInit(1000UL);
//	NVIC_SetPriority(SysTick_IRQn, 0x0);	

	Set_USBClock();
	USB_Interrupts_Config();
	USB_Init();
	
	IOInit();
	TIMInit();
	encoder_init();
//	dcmotor_init(7200, 3500);
	dcmotorctrl_init();

//	encoder_reset();

//	i = 2.0/3.0;
//	CDC_Send_DATA ("OK ",3);

  /* USARTx configured as follow:
        - BaudRate = 115200 baud  
        - Word Length = 8 Bits
        - One Stop Bit
        - No parity
        - Hardware flow control disabled (RTS and CTS signals)
        - Receive and transmit enabled
  */
#if 0
	USART_InitStructure.USART_BaudRate = 115200;
	USART_InitStructure.USART_WordLength = USART_WordLength_8b;
	USART_InitStructure.USART_StopBits = USART_StopBits_1;
	USART_InitStructure.USART_Parity = USART_Parity_No;
	USART_InitStructure.USART_HardwareFlowControl = USART_HardwareFlowControl_None;
	USART_InitStructure.USART_Mode = USART_Mode_Rx | USART_Mode_Tx;
	STM_EVAL_COMInit(COM1, &USART_InitStructure);
#endif
//  printf("\n\r %s", MESSAGE1);
//  printf(" %s", MESSAGE2);
//  printf(" %s\n\r", MESSAGE3);
  
	GPIO_SetBits(GPIOB,GPIO_Pin_9);

	dcmotor_on(1);

  /* Add your application code here
     */
//	xSemaphore = xSemaphoreCreateMutex(); 
//	xTaskCreate(accTask, (signed char* )"accTask", 1024*2, NULL, 3, NULL);
//	_freertos_preemtion_enable = 1;
//	xTaskCreate(vTerminalControlTask, "TerminalCtrl", 1024, NULL, 4, NULL);
	xTaskCreate( vLedBlinkBlue, (const signed char*)"Led Blink Task Blue", 
		STACK_SIZE_MIN, NULL, 1, NULL );
	xTaskCreate( vLedBlinkRed, (const signed char*)"Led Blink Task Red", 
		STACK_SIZE_MIN, NULL, 2, NULL );
	xTaskCreate( vSequenceControl, (const signed char*)"Led Blink Task Red", 
		STACK_SIZE_MIN, NULL, 3, NULL );
	vTaskStartScheduler();
	GPIO_SetBits(GPIOB,GPIO_Pin_8);
	GPIO_ResetBits(GPIOB,GPIO_Pin_9);

  /* Infinite loop */
  while (1)
  {
#if 0
		Delay(100);
		if(status_LED2 == 0){
			GPIO_ResetBits(GPIOB,GPIO_Pin_9);
			status_LED2 = 1;
		}else{
			GPIO_SetBits(GPIOB,GPIO_Pin_9);
			status_LED2 = 0;
		}
//		GPIO_SetBits(GPIOB,GPIO_Pin_9);
//		GPIO_ResetBits(GPIOB,GPIO_Pin_8);
#endif
	}
}


/************************ (C) COPYRIGHT STMicroelectronics *****END OF FILE****/

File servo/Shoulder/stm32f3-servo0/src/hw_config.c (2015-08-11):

/**
  ******************************************************************************
  * @file    hw_config.c
  * @author  MCD Application Team
  * @version V4.0.0
  * @date    21-January-2013
  * @brief   Hardware Configuration & Setup
  ******************************************************************************
  * @attention
  *
  * <h2><center>&copy; COPYRIGHT 2013 STMicroelectronics</center></h2>
  *
  * Licensed under MCD-ST Liberty SW License Agreement V2, (the "License");
  * You may not use this file except in compliance with the License.
  * You may obtain a copy of the License at:
  *
  *        http://www.st.com/software_license_agreement_liberty_v2
  *
  * Unless required by applicable law or agreed to in writing, software 
  * distributed under the License is distributed on an "AS IS" BASIS, 
  * WITHOUT WARRANTIES OR CONDITIONS OF ANY KIND, either express or implied.
  * See the License for the specific language governing permissions and
  * limitations under the License.
  *
  ******************************************************************************
  */


/* Includes ------------------------------------------------------------------*/

#include "stm32_it.h"
#include "usb_lib.h"
#include "usb_prop.h"
#include "usb_desc.h"
#include "hw_config.h"
#include "usb_pwr.h"


/* Private typedef -----------------------------------------------------------*/
/* Private define ------------------------------------------------------------*/
/* Private macro -------------------------------------------------------------*/
/* Private variables ---------------------------------------------------------*/
ErrorStatus HSEStartUpStatus;
USART_InitTypeDef USART_InitStructure;
EXTI_InitTypeDef EXTI_InitStructure;
uint8_t  USART_Rx_Buffer [USART_RX_DATA_SIZE]; 
uint32_t USART_Rx_ptr_in = 0;
uint32_t USART_Rx_ptr_out = 0;
uint32_t USART_Rx_length  = 0;

extern __IO uint32_t packet_sent;
extern __IO uint8_t Send_Buffer[VIRTUAL_COM_PORT_DATA_SIZE] ;
extern __IO  uint32_t packet_receive;
extern __IO uint8_t Receive_length;
uint8_t Receive_Buffer[64];
uint32_t Send_length;

uint8_t  USB_Tx_State = 0;
static void IntToUnicode (uint32_t value , uint8_t *pbuf , uint8_t len);
/* Extern variables ----------------------------------------------------------*/

extern LINE_CODING linecoding;

/* Private function prototypes -----------------------------------------------*/
/* Private functions ---------------------------------------------------------*/
/*******************************************************************************
* Function Name  : Set_System
* Description    : Configures Main system clocks & power
* Input          : None.
* Return         : None.
*******************************************************************************/
void Set_System(void)
{
#if !defined(STM32L1XX_MD) && !defined(STM32L1XX_HD) && !defined(STM32L1XX_MD_PLUS)
  GPIO_InitTypeDef GPIO_InitStructure;
#endif /* STM32L1XX_MD && STM32L1XX_XD */  

#if defined(USB_USE_EXTERNAL_PULLUP)
  GPIO_InitTypeDef  GPIO_InitStructure;
#endif /* USB_USE_EXTERNAL_PULLUP */ 
  
  /*!< At this stage the microcontroller clock setting is already configured, 
       this is done through SystemInit() function which is called from startup
       file (startup_stm32f10x_xx.s) before to branch to application main.
       To reconfigure the default setting of SystemInit() function, refer to
       system_stm32f10x.c file
     */   
#if defined(STM32L1XX_MD) || defined(STM32L1XX_HD)|| defined(STM32L1XX_MD_PLUS) || defined(STM32F37X) || defined(STM32F30X)
  /* Enable the SYSCFG module clock */
  RCC_APB2PeriphClockCmd(RCC_APB2Periph_SYSCFG, ENABLE);
#endif /* STM32L1XX_XD */ 
   
#if !defined(STM32L1XX_MD) && !defined(STM32L1XX_HD) && !defined(STM32L1XX_MD_PLUS) && !defined(STM32F37X) && !defined(STM32F30X)
  /* Enable USB_DISCONNECT GPIO clock */
  RCC_APB2PeriphClockCmd(RCC_APB2Periph_GPIO_DISCONNECT, ENABLE);

  /* Configure USB pull-up pin */
  GPIO_InitStructure.GPIO_Pin = USB_DISCONNECT_PIN;
  GPIO_InitStructure.GPIO_Speed = GPIO_Speed_50MHz;
  GPIO_InitStructure.GPIO_Mode = GPIO_Mode_Out_OD;
  GPIO_Init(USB_DISCONNECT, &GPIO_InitStructure);
#endif /* STM32L1XX_MD && STM32L1XX_XD */
   
#if defined(USB_USE_EXTERNAL_PULLUP)
  /* Enable the USB disconnect GPIO clock */
  RCC_AHBPeriphClockCmd(RCC_AHBPeriph_GPIO_DISCONNECT, ENABLE);

  /* USB_DISCONNECT used as USB pull-up */
  GPIO_InitStructure.GPIO_Pin = USB_DISCONNECT_PIN;
  GPIO_InitStructure.GPIO_Mode = GPIO_Mode_OUT;
  GPIO_InitStructure.GPIO_Speed = GPIO_Speed_2MHz;
  GPIO_InitStructure.GPIO_OType = GPIO_OType_PP;
  GPIO_InitStructure.GPIO_PuPd = GPIO_PuPd_NOPULL;
  GPIO_Init(USB_DISCONNECT, &GPIO_InitStructure);  
#endif /* USB_USE_EXTERNAL_PULLUP */
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

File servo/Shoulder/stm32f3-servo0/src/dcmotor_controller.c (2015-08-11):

#include "dcmotor_controller.h"
#include "dcmotor.h"
#include "encoder.h"
//#include "logg.h"
//#include "logger.h"
//#include "struct_id.h"

#include "FreeRTOS.h"
#include "semphr.h"
#include "task.h"
#include "queue.h"

//#include "uart.h"
//#include "uart_support.h"
//#include "xprintf.h"

static volatile int32_t _target_a = 0;
static volatile int32_t _a_error_prev = 0;
static volatile float _integral_a = 0.f;
//static volatile float _Kp = 0.6f;
//static volatile float _Kp = 1.0f;
static volatile float _Kp = 0.2f;
static volatile float _Kd = 0.f;
//static volatile float _Kd = 0.15f;
//static volatile float _Kd = 0.05f;
static volatile float _Ki = 0.f;
//static volatile float _Ki = 0.2f;
//static volatile float _Ki = 0.05f;
static volatile uint32_t _last_timestamp = 0;


//typedef struct {
//	StructID	id;
//	uint32_t timestamp;
//	int32_t target_a;
//	int32_t target_b;
//	int32_t encoder_a;
//	int32_t encoder_b;
//	int32_t motor_a;
//	int32_t motor_b;
//} DCMotorLog;

//static DCMotorLog	_log;

void dcmotorctrl_init(void) {
	_target_a = 0;
	_a_error_prev = 0;
	_integral_a = 0.f;
	_last_timestamp = 0;
	
//	uart_init(2, 115200);
	
//	memset(&_log, 0, sizeof(_log));
//	_log.id.id = STRUCT_ID_DCMOTOR;
//	_log.id.size = sizeof(_log);
	
	dcmotor_init(200, 80);
	dcmotor_set_a(0);
	dcmotorctrl_stop();
}

void dcmotorctrl_start(void) {
	dcmotor_on_a(true);
}

void dcmotorctrl_stop(void) {
	dcmotor_on_a(false);
}

#if 1

// DCMotor PID control

//void dcmotorctrl_update(void) {
int32_t dcmotorctrl_update(void) {
	float dt = 0.f;
	uint32_t now = xTaskGetTickCount();
  if (_last_timestamp != 0) {
		dt = (float)(now - _last_timestamp) / 1000.f;
	}
	_last_timestamp = now;
	
  int32_t a = encoder_get_a();
  int32_t a_error = _target_a - a;
  int32_t a_error_delta = a_error - _a_error_prev;
  _integral_a += (float)(a_error + _a_error_prev) * 0.5f * dt;
  _a_error_prev = a_error;
	int32_t motor_a = a_error * _Kp + _integral_a * _Ki + a_error_delta * _Kd;
  dcmotor_set_a(motor_a);
  
//    return a_error;
   return _target_a;

//	_log.timestamp = xTaskGetTickCount();
//	_log.target_a = _target_a;
//	_log.target_b = _target_b;
//	_log.encoder_a = a;
//	_log.encoder_b = b;
//	_log.motor_a = motor_a;
//	_log.motor_b = motor_b;
//	logger_append_log((const uint8_t*)&_log, sizeof(_log));

//	uart_write(2, (const uint8_t*)&_log, sizeof(_log));
}

void dcmotorctrl_set_motor_a_deg(float deg) {
//	_target_a = deg / 360.f * 4000.f;
//	_target_a = ((deg / 360.f) * 512.f)/3.0;
	_target_a = (deg / 360.f) * 256.f;
}


#else 

// for DC motor / encoder test

void dcmotorctrl_update(void) {
	static uint32_t t = 0;
	uint32_t now = xTaskGetTickCount();
	if (now - t > 1000) {
	  int32_t a = encoder_get_a();
//		printf("[Control] A:%8ld B:%8ld\n", a, b);
		t = now;
	}
	
//	_log.timestamp = xTaskGetTickCount();
//	_log.target_a = _target_a;
//	_log.target_b = _target_b;
//	_log.encoder_a = encoder_get_a();
//	_log.encoder_b = encoder_get_b();
//	_log.motor_a = 0;
//	_log.motor_b = 0;
//	logger_append_log((const uint8_t*)&_log, sizeof(_log));
}

void dcmotorctrl_set_motor_a_deg(float deg) {
	_target_a = deg;
  dcmotor_set_a(_target_a);
}


#endif

void dcmotorctrl_dump_params(void) {
//	loggf("[Control] Kp: %.3f", _Kp);
//	loggf("[Control] Ki: %.3f", _Ki);
//	loggf("[Control] Kd: %.3f", _Kd);
//	loggf("[Control] _target_a: %d (%.3fdeg)", _target_a, _target_a*360.f/4000.f);
//	loggf("[Control] encoder_a: %d", encoder_get_a());
//	loggf("[Control] _target_b: %d (%.3fdeg)", _target_b, _target_b*360.f/4000.f);
//	loggf("[Control] encoder_b: %d", encoder_get_b());
}

void dcmotorctrl_dump_values(void) {
//	uint32_t timestamp = xTaskGetTickCount();
//	printf("%ld\t%ld\t%ld\t%ld\t%ld\n", timestamp, _target_a, _target_b, encoder_get_a(), encoder_get_b());
}

void dcmotorctrl_set_kp(float kp) {
	_Kp = kp;
}

void dcmotorctrl_set_ki(float ki) {
	_Ki = ki;
}

void dcmotorctrl_set_kd(float kd) {
	_Kd = kd;
}

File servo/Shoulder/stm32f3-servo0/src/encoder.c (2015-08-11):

#include "encoder.h"

#include "FreeRTOS.h"
#include "semphr.h"
#include "task.h"
#include "queue.h"

// based on http://www.micromouseonline.com/2013/02/16/quadrature-encoders-with-the-stm32f4/

/*
* definitions for the quadrature encoder pins
*/

// A Channels
// JP-6 3
#define ENCLA_PIN               GPIO_Pin_8
#define ENCLA_GPIO_PORT         GPIOA
#define ENCLA_GPIO_CLK          RCC_AHBPeriph_GPIOA
#define ENCLA_SOURCE            GPIO_PinSource8
#define ENCLA_AF                GPIO_AF_2

// JP-6 4
#define ENCLB_PIN               GPIO_Pin_9
#define ENCLB_GPIO_PORT         GPIOA
#define ENCLB_GPIO_CLK          RCC_AHBPeriph_GPIOA
#define ENCLB_SOURCE            GPIO_PinSource9
#define ENCLB_AF                GPIO_AF_2

// determine the timers to use
#define ENCL_TIMER              TIM2
#define ENCL_TIMER_CLK          RCC_APB1Periph_TIM2
//#define ENCR_TIMER              TIM4
//#define ENCR_TIMER_CLK          RCC_APB1Periph_TIM4

static volatile int32_t _leftTotal;
static volatile int32_t _rightTotal;
static volatile int16_t _leftEncoder;
static volatile int16_t _rightEncoder;


/*
 * Configure two timers as quadrature encoder counters. 
 * Details of which timers should be used are
 * in the project hardware header file.
 * Most timers can be used if channels 1 and 2 are available on pins.
 * The timers are mostly 16 bit. Timers can be set to 32 bit but they are
 * not very convenient for IO pins so the counters are simply set to to
 * 16 bit counting regardless.
 * A mouse needs 32 bits of positional data and, since it also needs the
 * current speed, distance is not maintained by the encoder code but will
 * be looked after by the motion control code.
 * The counters are set to X4 mode. The only alternative is X2 counting.
 */
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

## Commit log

2015-08-11 Make Tokyo 2015 Var.
    [elbow_00c_r13a.dxf, elbow_02a_r13a.dxf, encorder_org_23.dxf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]
2015-08-11 file add
    [elbow_071a_ascii.dxf, elbow_072_ascii.dxf, encorder_org_26a.dxf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]

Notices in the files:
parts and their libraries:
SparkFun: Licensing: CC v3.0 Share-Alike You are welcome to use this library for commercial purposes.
